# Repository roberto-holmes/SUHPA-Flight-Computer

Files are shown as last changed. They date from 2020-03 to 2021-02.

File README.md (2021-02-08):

# SUHPA Avionics

Currently divided into CRASH (Controls, Radio, and Avionics for Southampton HPA) that receives input from the pilot and sends it to Pod that controls the servos.

## Software
TODO:
- Varying frequency beep as trim value changes
- Accelerating trim input
- Add average update rate to display

Known issues:
- SD card doesn't reinitialize if it disconects as this would cause the device to only transmit packets every couple of seconds
- Packet loss is not representative of the number of packets being received by Pod as the ACK packages being sent back are the ones getting lost. Pod has to send them at a lower power for some reason causing this issue.

## Hardware

### CRASH 

v1.0
- Status: Completed
- Issues:
   * Stress relief holes for battery cables are too small
   * Middle support holes are not required
   * Circle cutout is not quite aligned
   * Square cutout could have more clearance on the left

### Pod
v1.0
- Status: Completed
- Issues: 
   * Short between 5v_Servo and GND at the BEC connector
   * Insufficient spacing between buzzer and balance connector
   * Balance connector keeps board powered (should be replaced with just measuring the voltage of V_bat)

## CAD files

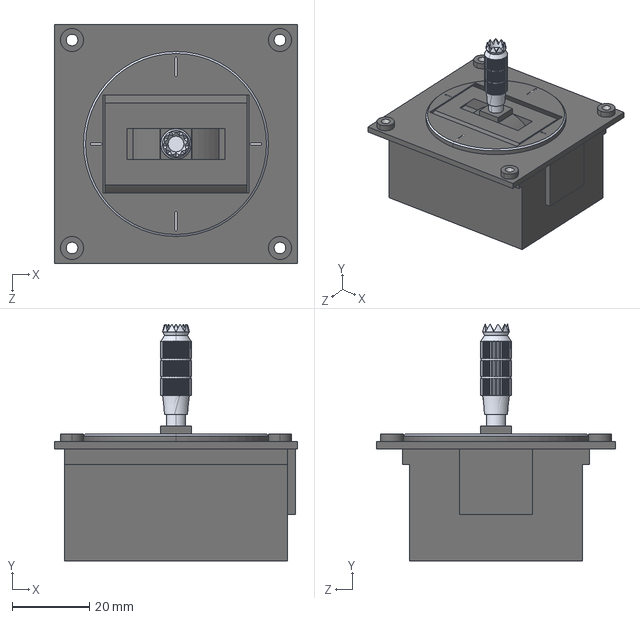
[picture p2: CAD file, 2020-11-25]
Altium/Crash/CRASH/FrSky M9 Gimbal.STEP
63.1 x 61.5 x 62.0 mm

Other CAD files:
Solidworks/FrSky M9 Gimbal.SLDPRT

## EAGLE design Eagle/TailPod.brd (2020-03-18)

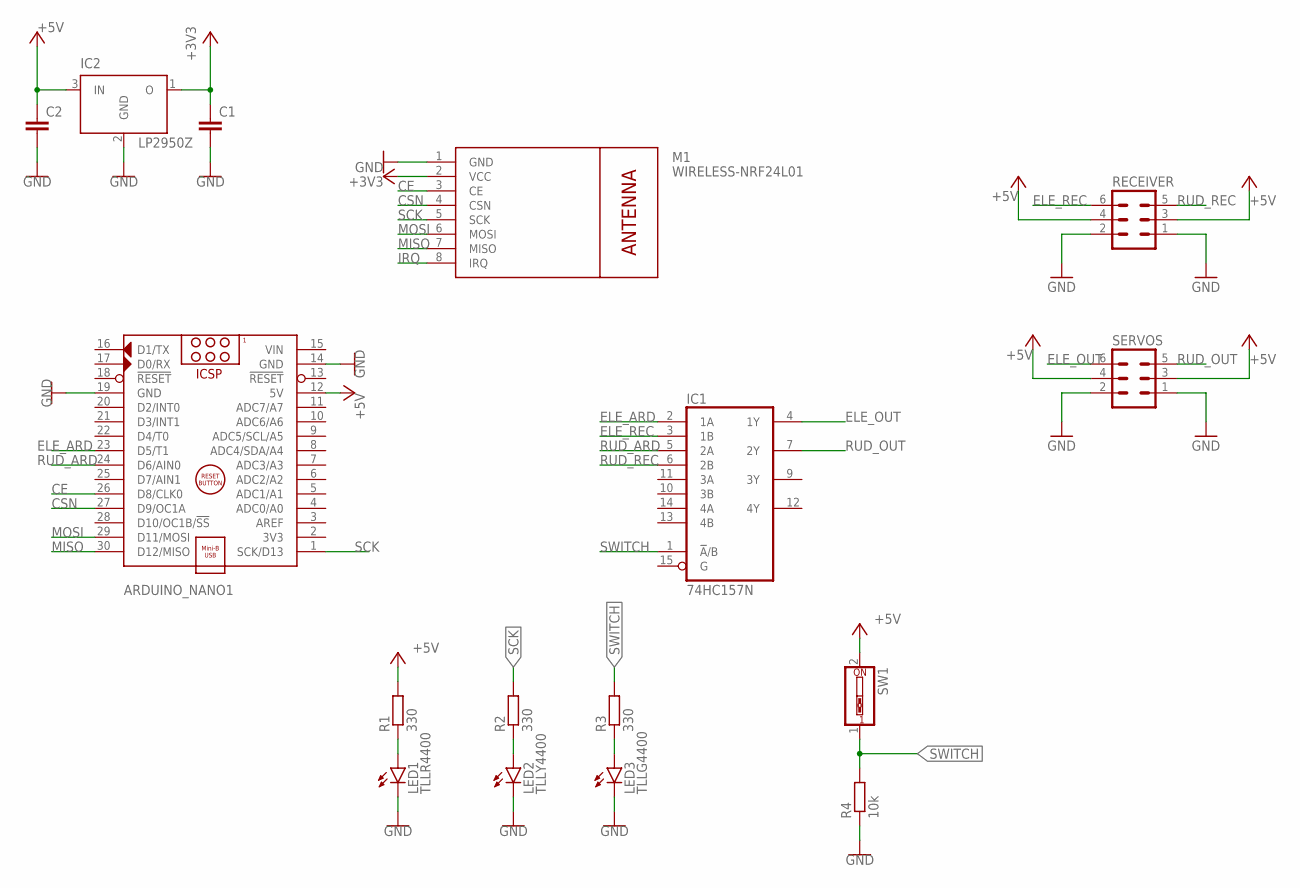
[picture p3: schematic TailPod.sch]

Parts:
ARDUINO_NANO1: ARDUINO_NANO
C1, C2: C2,5-3; C2.5-3
IC1: 74HC157N; DIL16
IC2: LP2950Z; TO92
LED1: TLLR4400; LED3MM
LED2: TLLY4400; LED3MM
LED3: TLLG4400; LED3MM
M1: WIRELESS-NRF24L01
R1, R2, R3: 330; 0204/7
R4: 10k; 0204/7
RECEIVER: MA03-2
SERVOS: MA03-2
SW1: SW_DIP-1; EDG-01

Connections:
+3V3: C1.1, IC2.1 (O), M1.2 (VCC)
+5V: ARDUINO_NANO1.12 (5V), C2.1, IC2.3 (IN), R1.2, RECEIVER.3, RECEIVER.4, SERVOS.3, SERVOS.4, SW1.2
CE: ARDUINO_NANO1.26 (D8/CLK0), M1.3 (CE)
CSN: ARDUINO_NANO1.27 (D9/OC1A), M1.4 (CSN)
ELE_ARD: ARDUINO_NANO1.23 (D5/T1), IC1.2 (1A)
ELE_OUT: IC1.4 (1Y), SERVOS.6
ELE_REC: IC1.3 (1B), RECEIVER.6
GND: ARDUINO_NANO1.14 (GND), ARDUINO_NANO1.19 (GND), C1.2, C2.2, IC1.8 (GND), IC2.2 (GND), LED1.K (C), LED2.K (C), LED3.K (C), M1.1 (GND), R4.1, RECEIVER.1, RECEIVER.2, SERVOS.1, SERVOS.2
IRQ: M1.8 (IRQ)
MISO: ARDUINO_NANO1.30 (D12/MISO), M1.7 (MISO)
MOSI: ARDUINO_NANO1.29 (D11/MOSI), M1.6 (MOSI)
unnamed: LED1.A, R1.1
unnamed: LED2.A, R2.1
unnamed: LED3.A, R3.1
RUD_ARD: ARDUINO_NANO1.24 (D6/AIN0), IC1.5 (2A)
RUD_OUT: IC1.7 (2Y), SERVOS.5
RUD_REC: IC1.6 (2B), RECEIVER.5
SCK: ARDUINO_NANO1.1 (SCK/D13), M1.5 (SCK), R2.2
SWITCH: IC1.1 (!A!/B), R3.2, R4.2, SW1.1
VCC: IC1.16 (VCC)
VIN: ARDUINO_NANO1.15 (VIN)

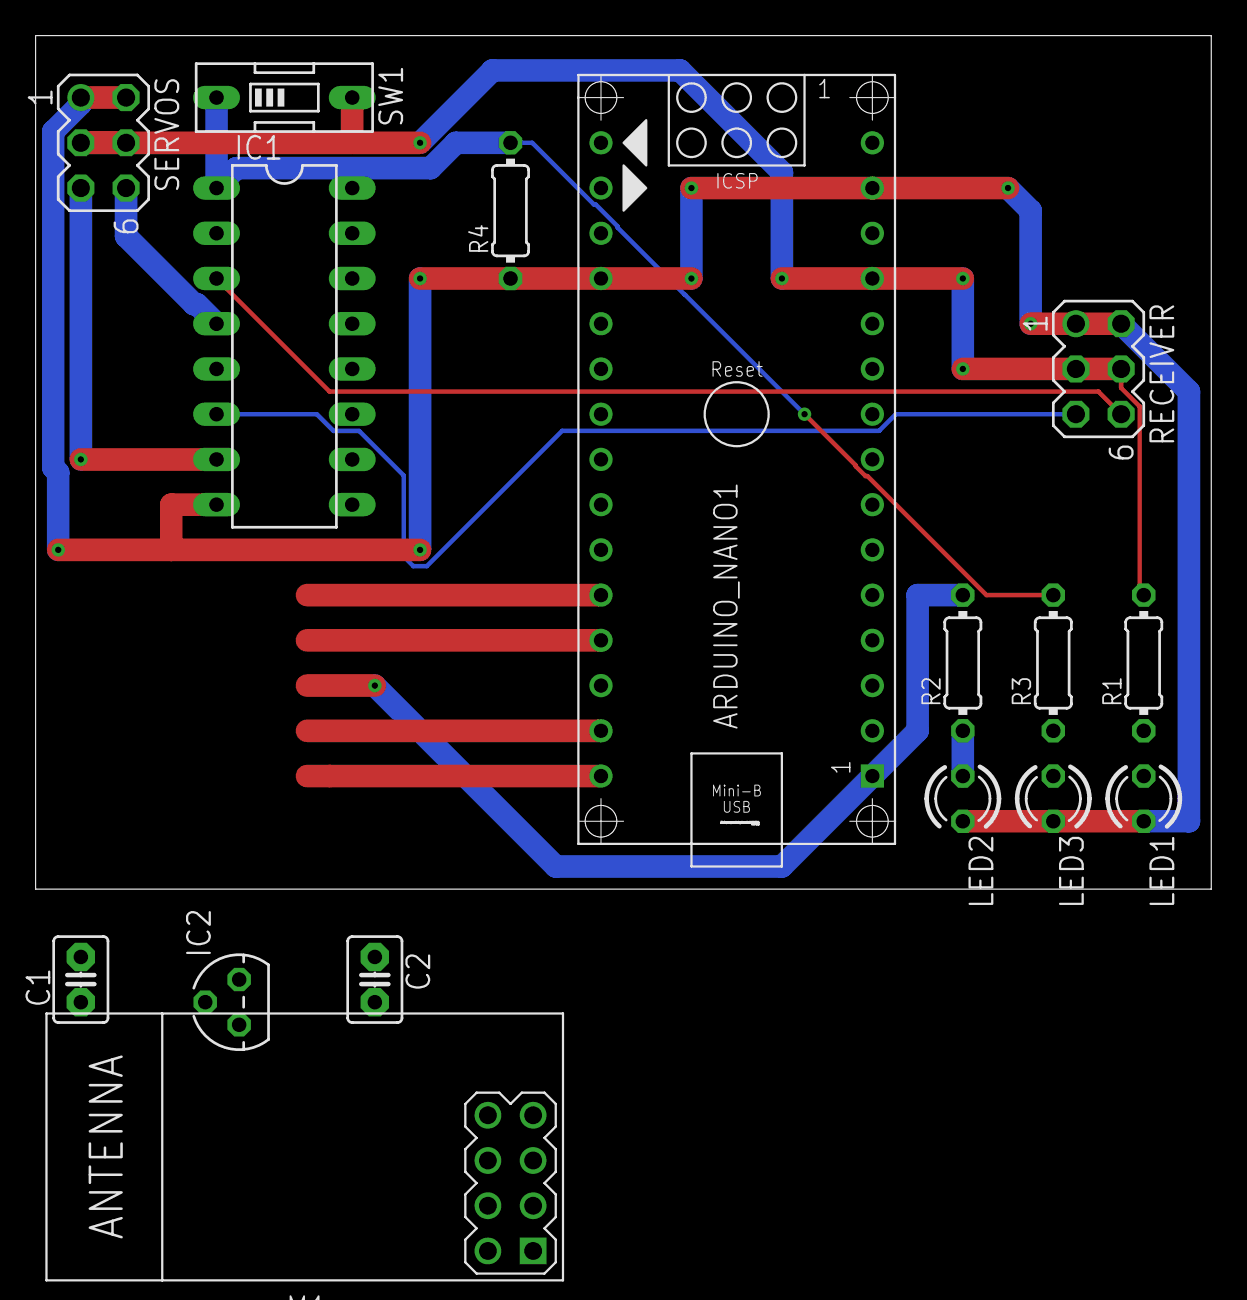
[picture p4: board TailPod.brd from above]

Board: 2 copper layers, 66.0 x 47.9 mm, 16 parts (0 on the bottom side), 18 nets.

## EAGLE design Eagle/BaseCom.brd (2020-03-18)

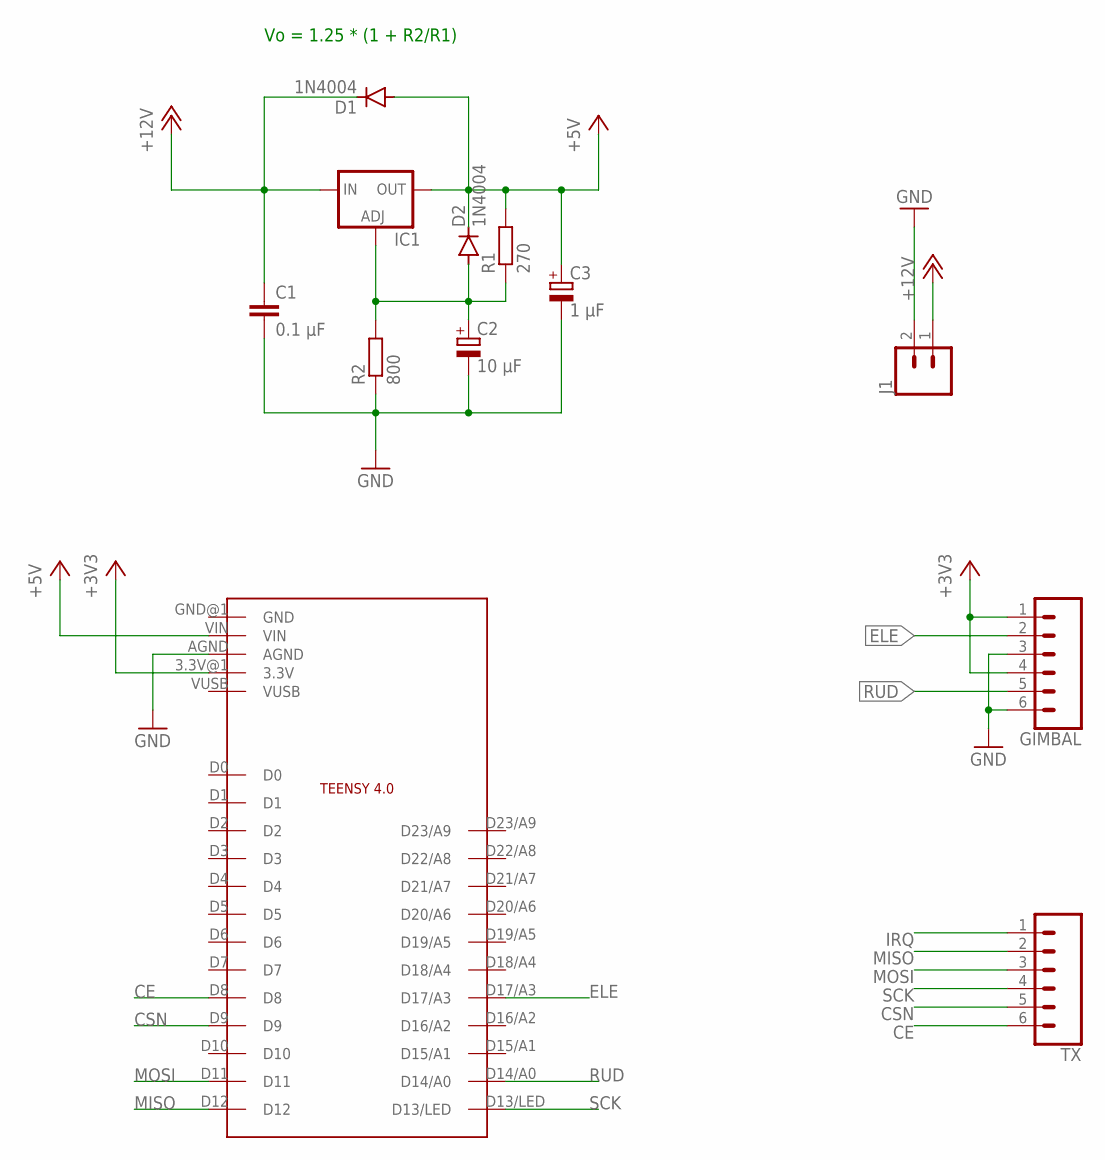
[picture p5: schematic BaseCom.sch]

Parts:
C1: 0.1 µF; C2.5-5
C2: 10 µF; E1,8-4
C3: 1 µF; E1,8-4
D1, D2: 1N4004; DO41-10
GIMBAL: CONN_06SILK_FEMALE_PTH; 1X06
IC1: LM317TL; 317TL
J1: CONN_02POLAR; MOLEX-1X2
R1: 270; 0204/7
R2: 800; 0204/7
TX: CONN_06SILK_FEMALE_PTH; 1X06
U$1: TEENSY4.0_SIMPLE

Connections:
+3V3: GIMBAL.1, GIMBAL.4, U$1.3.3V@1 (3.3V)
+5V: C3.+, D1.A, D2.C, IC1.2 (OUT), R1.2, U$1.VIN
+12V: C1.1, D1.C, IC1.3 (IN), J1.1
CE: TX.6, U$1.D8
CSN: TX.5, U$1.D9
ELE: GIMBAL.2, U$1.D17/A3
GND: C1.2, C2.-, C3.-, GIMBAL.3, GIMBAL.6, J1.2, R2.1, U$1.AGND
IRQ: TX.1
MISO: TX.2, U$1.D12
MOSI: TX.3, U$1.D11
unnamed: C2.+, D2.A, IC1.1 (ADJ), R1.1, R2.2
RUD: GIMBAL.5, U$1.D14/A0
SCK: TX.4, U$1.D13/LED

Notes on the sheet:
Vo = 1.25 * (1 + R2/R1)

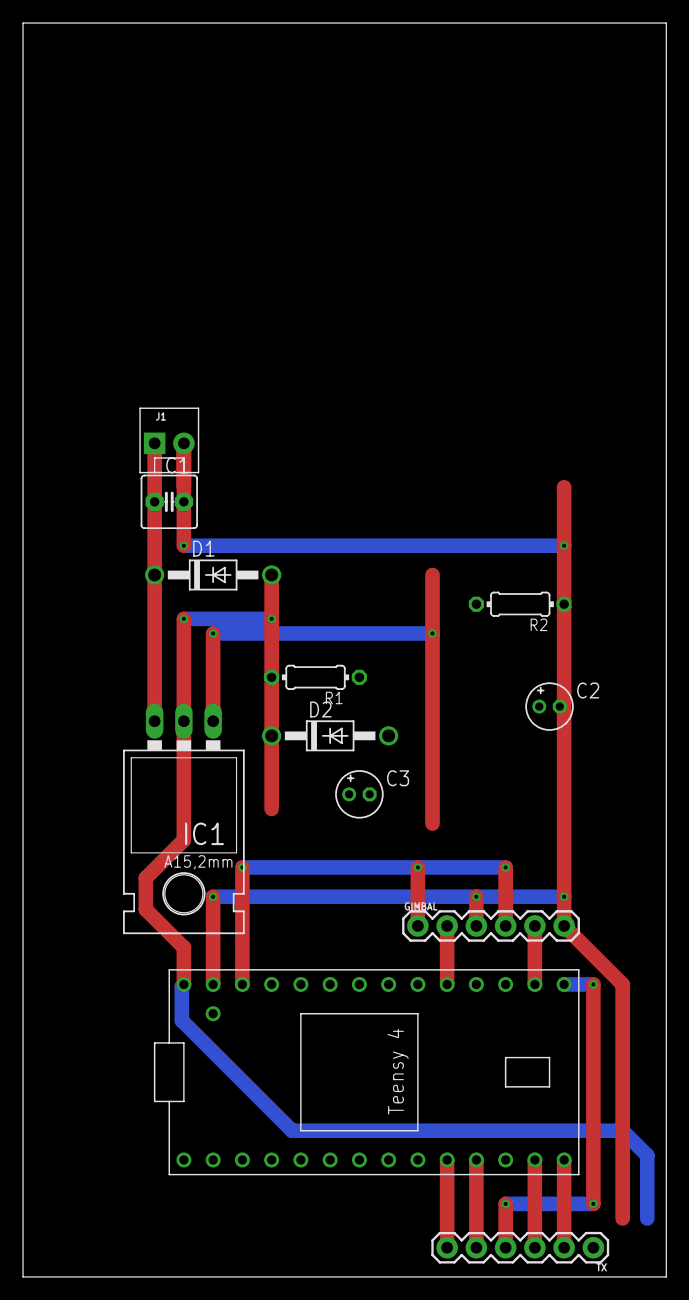
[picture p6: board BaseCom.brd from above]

Board: 2 copper layers, 55.9 x 108.9 mm, 12 parts (0 on the bottom side), 12 nets.

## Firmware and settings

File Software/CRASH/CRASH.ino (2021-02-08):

#include <Adafruit_BMP3XX.h>
#include <Adafruit_BNO055.h>
#include <EEPROM.h>
#include <RF24.h>
#include <SPI.h>
#include <SdFat.h>
#include <TimeLib.h>
#include <Wire.h>
#include <avr/pgmspace.h>
#include <math.h>
#include <nRF24L01.h>
#include <printf.h>
#include <stdint.h>
#include <usb_serial.h>
#include <util/crc16.h>

#include "Display.h"
#include "Record.h"

//#define VERBOSE_LOGGING

int leds[] = {22, 21, 40, 39, 38, 37, 35, 0, 1, 2, 3, 4};

// Trim LEDs
#define vertMin 4
#define vertLow 3
#define vertMid 2
#define vertHigh 1
#define vertMax 0

#define horizMin 40
#define horizLow 39
#define horizMid 38
#define horizHigh 37
#define horizMax 35

// Trim inputs
#define trimUp 31
#define trimDown 30

#define trimLeft 28
#define trimRight 29

// Stick inputs
#define stickVert 14
#define stickHoriz 15

// Battery voltage (If you multiply by 4.09)
#define batSense 23

// Radio
#define radioCE 27
#define radioCSN 26
#define radioINT 25
#define PACKAGE_SIZE 8
#define ACK_PAYLOAD_SIZE 2
#define PACKET_LOSS_SAMPLE_SIZE 100
#define PING_SAMPLE_SIZE 100

// Display
#define displayFR 41
#define displayCSB 16
#define displayRSTB 17
#define displayDC 20

// Other outputs
#define buzzer 33
#define led1 22
#define led2 21

// EEPROM
// There are limited write cycles to any address in EEPROM
// It should be about 100000 cycles, but in theory it could be be a problem
// If so comment out this line to dissable it
#define ENABLE_EEPROM

// You can also change to a different address as the limitation is per address not total
// Also these address need to be at least 4 apart as the trim values are integers (although they don't really need to be)
#define EEPROM_VERT_TRIM_ADDRESS 0
#define EEPROM_HORIZ_TRIM_ADDRESS 4

// Buzzer
int beepStopTime = 0;
bool beepOn = false;

// Values for battery voltage calculations
const float v100 = 3 * 4.2;
const float v0 = 3 * 3.5;
const float batVoltFactor = (3.3 * 4.09) / 1024;
float batPercent;

// PWM range (Absolute max 588 to 2400 ish)
const int vertMaxVal = 2200;
const int vertMinVal = 750;
const int horizMaxVal = 2200;
const int horizMinVal = 750;
float vertZero, horizZero;

// Stick input range
const int vertStickMax = 107;
const int vertStickMin = 910;
const int horizStickMax = 107;
const int horizStickMin = 905;
float vertStickZero, horizStickZero;

const float vertStickMultiplier = 1.0;
const float horizStickMultiplier = 1.0;
float vertStickRes, horizStickRes;

// Number of Trim steps / 2
const int vertSteps = 99;
const int horizSteps = 99;
float vertRes, horizRes;

// Values to store Trim and PWM
int vertTrim = 0;
int horizTrim = 0;
int vertVal = 0;
int horizVal = 0;

// Store state of trim buttons
bool trimUpDown = false;
bool trimDownDown = false;
bool trimLeftDown = false;
bool trimRightDown = false;

// Values for debouncing
unsigned long trimUpLastDebounceTime = 0;
unsigned long trimDownLastDebounceTime = 0;
unsigned long trimLeftLastDebounceTime = 0;
unsigned long trimRightLastDebounceTime = 0;

unsigned long trimUpLastPressTime = 0;
unsigned long trimDownLastPressTime = 0;
unsigned long trimLeftLastPressTime = 0;
unsigned long trimRightLastPressTime = 0;

const unsigned long debounceDelay = 50;
const unsigned long holdDelay = 250;
const unsigned long holdDelayCentre = 500;

// Radio Setup
RF24 radio(radioCE, radioCSN);
uint8_t address[][6] = {"CRASH", "Poddd"};
byte package[PACKAGE_SIZE];

// Variables frequency of communication
const unsigned long txInterval = 10;
unsigned long lastTXMillis;

// Control when the display gets updated
const unsigned long displayUpdateInterval = 20;
unsigned long lastDisplayUpdateMillis;

// Variables for calculating packet loss
bool ack[PACKET_LOSS_SAMPLE_SIZE];
int ackPos = 0;
int truers = 0;
float packetLoss;  // Fraction of packets that don't receive ack

// Variables for calculating return trip time
unsigned long pingArray[PACKET_LOSS_SAMPLE_SIZE];
int pingPos = 0;
float ping;	 // Average return trip time in ms

// Sensors
#define IMU_I2C_ADDRESS BNO055_ADDRESS_A
Adafruit_BNO055 imuDevice = Adafruit_BNO055(0, IMU_I2C_ADDRESS);
Adafruit_BMP3XX barometerDevice = Adafruit_BMP3XX();
DataRecord currentSensorData;
const unsigned long sensorReadInterval = 50;
unsigned long lastSensorUpdateMillis;

// Storage
#define STORAGE_DATA_DIRECTORY "Data"
#define STORAGE_FILE_NAME_FORMAT "Data/XXXX.csv\0"
#define STORAGE_FILE_NAME_LENGTH 14
#define STORAGE_FILE_NAME_NUMBER_START 5
#define STORAGE_FILE_NAME_MAX_NUMBER 9999

SdExFat sdio;
ExFile sdFile;
char* fileName = NULL;
bool sdCardInitialised = false;
SdioConfig sdConfig = SdioConfig();

// the setup routine runs once when you press reset:
void setup()
{
	Display::Init();
	initSensors();
	initSD();

	pinMode(vertMin, OUTPUT);
	pinMode(vertLow, OUTPUT);
	pinMode(vertMid, OUTPUT);
	pinMode(vertHigh, OUTPUT);
	pinMode(vertMax, OUTPUT);

	pinMode(horizMin, OUTPUT);
	pinMode(horizLow, OUTPUT);
	pinMode(horizMid, OUTPUT);
	pinMode(horizHigh, OUTPUT);
	pinMode(horizMax, OUTPUT);
	pinMode(buzzer, OUTPUT);

	pinMode(trimUp, INPUT);
	pinMode(trimDown, INPUT);
	pinMode(trimLeft, INPUT);
	pinMode(trimRight, INPUT);

	pinMode(stickVert, INPUT);
	pinMode(stickHoriz, INPUT);

	pinMode(batSense, INPUT);

	// Ensure trim LEDs are off
	digitalWrite(vertMin, LOW);
	digitalWrite(vertLow, LOW);
	digitalWrite(vertMid, LOW);
	digitalWrite(vertHigh, LOW);
	digitalWrite(vertMax, LOW);
	digitalWrite(horizMin, LOW);
	digitalWrite(horizLow, LOW);
	digitalWrite(horizMid, LOW);
	digitalWrite(horizHigh, LOW);
	digitalWrite(horizMax, LOW);

	pinMode(led1, OUTPUT);
	pinMode(led2, OUTPUT);
	pinMode(13, OUTPUT);

	for (int i = 0; i < 11; i++)
	{
		digitalWrite(leds[i], HIGH);
		delay(100);
		digitalWrite(leds[i], LOW);
	}

	for (int i = 12 - 1; i >= 1; i--)
	{
		digitalWrite(leds[i], HIGH);
		delay(100);
		digitalWrite(leds[i], LOW);
	}

	digitalWrite(leds[0], HIGH);
	delay(200);
	digitalWrite(leds[0], LOW);

	vertRes = (vertMaxVal - vertMinVal) / (2.0 * (vertSteps));
	horizRes = (horizMaxVal - horizMinVal) / (2.0 * (horizSteps));

	vertStickZero = (vertStickMax + vertStickMin) / 2.0;
	horizStickZero = (horizStickMax + horizStickMin) / 2.0;

	vertZero = (vertMaxVal + vertMinVal) / 2.0;
	horizZero = (horizMaxVal + horizMinVal) / 2.0;

	vertStickRes = vertStickMultiplier * (vertMaxVal - vertMinVal) / 2.0;
	horizStickRes = horizStickMultiplier * (horizMaxVal - horizMinVal) / 2.0;

	// Radio is not responding -> turn on warning LED
	if (!radio.begin())
	{
		digitalWrite(led2, HIGH);
	}

	// Initialise ack array
	for (int i = 0; i < PACKET_LOSS_SAMPLE_SIZE; i++)
		ack[i] = true;

	radio.setPALevel(RF24_PA_MAX);

	// Set up ack payloads
	radio.enableDynamicPayloads();
	radio.enableAckPayload();

	// Set up pipes
	radio.openWritingPipe(address[0]);
	radio.openReadingPipe(1, address[1]);

	// Put radio in TX mode
	radio.stopListening();

	lastTXMillis = millis();
	lastSensorUpdateMillis = millis();
	lastDisplayUpdateMillis = millis();

	readFromEEPROM();

	updateVertTrim(0);
	updateHorizTrim(0);
}

//uint32_t lastTime = 0;
//int counter = 0;

// the loop routine runs over and over again forever:
void loop()
{
	// Use the test how often the loop updates
	// counter++;
	// if (counter >= 100)
	// {
	// 	uint32_t currentTime = millis ();
	// 	Serial.println ((currentTime - lastTime) / counter);
	// 	lastTime = currentTime;
	// 	counter = 0;
	// }

	// Asynchronous beep
	if (beepOn && millis () >= (uint32_t)beepStopTime)
	{
		analogWrite (buzzer, 0);
		beepOn = false;
	}

	// Calculate battery state
	float batVoltage = analogRead(batSense) * batVoltFactor;
	batPercent = constrain(map(batVoltage, v0, v100, 0.0, 1.0), 0.0, 1.0);
	if (batPercent < .25)
		digitalWrite(led1, HIGH);
	else
		digitalWrite(led1, LOW);

	// Read Stick inputs and normalise
	float vertStickValue = -2.0 * (analogRead(stickVert) - vertStickZero) / (vertStickMax - vertStickMin);
	float horizStickValue = 2.0 * (analogRead(stickHoriz) - horizStickZero) / (horizStickMax - horizStickMin);

	// Calculate PWM values in both axis by combining stick inputs with trim
	float tempVertVal = vertStickValue * vertStickRes - vertTrim * vertRes + vertZero;
	float tempHorizVal = horizStickValue * horizStickRes - horizTrim * horizRes + horizZero;

	vertStickValue = constrain(vertStickValue, -1, 1);
	horizStickValue = constrain(horizStickValue, -1, 1);

	vertVal = constrain(tempVertVal, vertMinVal, vertMaxVal);
	horizVal = constrain(tempHorizVal, horizMinVal, horizMaxVal);

	// Check if button is being pressed
	if (digitalRead(trimUp))
	{
		// Debounce and check if the button is being held down
		if ((!trimUpDown || (vertTrim != 0 && millis() > trimUpLastPressTime + holdDelay) || (vertTrim == 0 && millis() > trimUpLastPressTime + holdDelayCentre)) && millis() > trimUpLastPressTime + debounceDelay)
		{
			trimUpLastPressTime = millis();
			trimUpDown = true;
			// vertTrim++;
			updateVertTrim(1);
		}
	}
	else
	{
		trimUpDown = false;
	}

	if (digitalRead(trimDown))
	{
		if ((!trimDownDown || (vertTrim != 0 && millis() > trimDownLastPressTime + holdDelay) || (vertTrim == 0 && millis() > trimDownLastPressTime + holdDelayCentre)) && millis() > trimDownLastPressTime + debounceDelay)
		{
			trimDownLastPressTime = millis();
			trimDownDown = true;
			// vertTrim--;
			updateVertTrim(-1);
		}
	}
	else
	{
		trimDownDown = false;
	}

	if (digitalRead(trimLeft))
	{
		if ((!trimLeftDown || (horizTrim != 0 && millis() > trimLeftLastPressTime + holdDelay) || (horizTrim == 0 && millis() > trimLeftLastPressTime + holdDelayCentre)) && millis() > trimLeftLastPressTime + debounceDelay)
		{
			trimLeftLastPressTime = millis();
			trimLeftDown = true;
			// horizTrim--;
			updateHorizTrim(-1);
		}
	}
	else
	{
		trimLeftDown = false;
	}

	if (digitalRead(trimRight))
	{
		if ((!trimRightDown || (horizTrim != 0 && millis() > trimRightLastPressTime + holdDelay) || (horizTrim == 0 && millis() > trimRightLastPressTime + holdDelayCentre)) && millis() > trimRightLastPressTime + debounceDelay)
		{
			trimRightLastPressTime = millis();
			trimRightDown = true;
			// horizTrim++;
			updateHorizTrim(1);
		}
	}
	else
	{
		trimRightDown = false;
	}

	unsigned long currentMillis = millis();

	// Decide whether it is time to transmit
	if (currentMillis - lastTXMillis > txInterval)
	{
		lastTXMillis = currentMillis;
		// Transmit PWM values
		transmit(vertVal, horizVal);
	}

	// Decide whether it is time to update screen
	if (currentMillis - lastDisplayUpdateMillis > displayUpdateInterval)
	{
		lastDisplayUpdateMillis = currentMillis;
		Display::Update(vertVal, horizVal, horizMinVal, horizMaxVal, vertMinVal, vertMaxVal, horizTrim, vertTrim, batPercent, ping, packetLoss, sdCardInitialised);
	}

	// Decide whether it is time to read and save sensor data
	if (currentMillis - lastSensorUpdateMillis > sensorReadInterval)
	{
		lastSensorUpdateMillis = currentMillis;

		// Read sensor data
		readFromSensors();

		// Use to print data to console
		//currentSensorData.printData ();

		// Save the data to SD card
		saveCurrentDataRecord();
	}
}

void beep(int level, int time)
{
	analogWrite(buzzer, 64 + (level * 16));
	beepStopTime = millis() + time;
	beepOn = true;
}

void updateVertTrim(int trimInput)
{
	if (trimInput != 0)
	{
		if (vertTrim + trimInput <= vertSteps && vertTrim + trimInput >= -vertSteps)
		{
			vertTrim += trimInput;
			beep(0, 100);
		}
	}

	digitalWrite(vertMin, LOW);
	digitalWrite(vertLow, LOW);
	digitalWrite(vertMid, LOW);
	digitalWrite(vertHigh, LOW);
	digitalWrite(vertMax, LOW);

	if (vertTrim == -vertSteps)
		digitalWrite(vertMin, HIGH);
	else if (vertTrim < 0)
		digitalWrite(vertLow, HIGH);
	else if (vertTrim == 0)
		digitalWrite(vertMid, HIGH);
	else if (vertTrim < vertSteps)
		digitalWrite(vertHigh, HIGH);
	else if (vertTrim == vertSteps)
		digitalWrite(vertMax, HIGH);

	writeToEEPROM();
}

void updateHorizTrim(int trimInput)
{
	if (trimInput != 0)
	{
		if (horizTrim + trimInput <= horizSteps && horizTrim + trimInput >= -horizSteps)
		{
			horizTrim += trimInput;
			beep(0, 100);
		}
	}

	digitalWrite(horizMin, LOW);
	digitalWrite(horizLow, LOW);
	digitalWrite(horizMid, LOW);
	digitalWrite(horizHigh, LOW);
	digitalWrite(horizMax, LOW);

	if (horizTrim == -horizSteps)
		digitalWrite(horizMin, HIGH);
	else if (horizTrim < 0)
		digitalWrite(horizLow, HIGH);
	else if (horizTrim == 0)
		digitalWrite(horizMid, HIGH);
	else if (horizTrim < horizSteps)
		digitalWrite(horizHigh, HIGH);
	else if (horizTrim == horizSteps)
		digitalWrite(horizMax, HIGH);

	writeToEEPROM();
}

void transmit(float ele, float rud)
{
	memcpy(package + 0, &ele, 4);
	memcpy(package + 4, &rud, 4);

	unsigned long start_timer = micros();  // start the timer
	bool report = radio.write(&package, PACKAGE_SIZE);	// transmit & save the report
	unsigned long end_timer = micros();	 // end the timer

	if (report)
	{
		//Serial.print(F("Transmission successful! "));  // payload was delivered
		// Serial.print(F("Time to transmit = "));
		// Serial.println(end_timer - start_timer);  // print the timer result
		// Serial.print(F(" us. Sent: "));
		// Serial.println(payload);	// print the outgoing message

		ack[ackPos] = true;
		pingArray[pingPos++] = end_timer - start_timer;
		pingPos %= PING_SAMPLE_SIZE;

		uint8_t pipe;
		if (radio.available(&pipe))
		{  // is there an ACK payload? grab the pipe number that received it
			byte received[ACK_PAYLOAD_SIZE];
			radio.read(&received, sizeof(received));  // get incoming ACK payload
			// Serial.print(F(" Received "));
			// Serial.print(radio.getDynamicPayloadSize());  // print incoming payload size
			// Serial.print(F(" bytes on pipe "));
			// Serial.print(pipe);	 // print pipe number that received the ACK
			// Serial.print(F(": "));
			// Serial.println(received);
		}
		else
		{
#if VERBOSE_LOGGING
			Serial.println (F ("Received: an empty ACK packet, ")); // empty ACK packet received
#endif
		}
	}
	else
	{
#if VERBOSE_LOGGING
		Serial.println (F ("Transmission failed or timed out, ")); // payload was not delivered
#endif
		ack[ackPos] = false;
	}

	// Calculate average ping over sample size
	ping = 0;
	for (int i = 0; i < PING_SAMPLE_SIZE; i++)
		ping += pingArray[i];
	ping /= (float)PING_SAMPLE_SIZE;
	ping /= 1000.;	// Convert from us to ms;

	// Calculate packet loss over sample size
	++ackPos %= PACKET_LOSS_SAMPLE_SIZE;
	truers = 0;
	for (int i = 0; i < PACKET_LOSS_SAMPLE_SIZE; i++)
	{
		if (ack[i])
			truers++;
	}
	packetLoss = 1 - (float)truers / (float)PACKET_LOSS_SAMPLE_SIZE;

	//Serial.print("Packet Loss: ");
	//Serial.print(packetLoss);
	//Serial.print(", Ping: ");
	//Serial.println(ping);
}

void readFromEEPROM()
{
#ifdef ENABLE_EEPROM

	// Read in the values
	vertTrim = readIntToEEPROM(EEPROM_VERT_TRIM_ADDRESS);
	horizTrim = readIntToEEPROM(EEPROM_HORIZ_TRIM_ADDRESS);

	// Validate the values
	// If they are not correct, give them default values
	// This is needed if the EEPROM gets corrupted
	if (vertTrim > vertSteps || vertTrim < -vertSteps) vertTrim = 0;
	if (horizTrim > horizSteps || horizTrim < -horizSteps) horizTrim = 0;

#endif	// ENABLE_EEPROM
}

void writeToEEPROM()
{
#ifdef ENABLE_EEPROM

	writeIntToEEPROM(EEPROM_VERT_TRIM_ADDRESS, vertTrim);
	writeIntToEEPROM(EEPROM_HORIZ_TRIM_ADDRESS, horizTrim);

#endif	// ENABLE_EEPROM
}

void writeIntToEEPROM(int address, int value)
{
	// Use the update method, so that we don't write to the EEPROM unless it is needed
	EEPROM.update(address + 0, (byte)(value));
	EEPROM.update(address + 1, (byte)(value >> 8));
	EEPROM.update(address + 2, (byte)(value >> 16));
	EEPROM.update(address + 3, (byte)(value >> 24));
}

int readIntToEEPROM(int address)
{
	int value = 0;

	value |= EEPROM.read(address);
	value |= EEPROM.read(address + 1) << 8;
	value |= EEPROM.read(address + 2) << 16;
	value |= EEPROM.read(address + 3) << 24;

	return value;
}

void initSensors()
{
	imuInit();
	barometerInit();
}

void readFromSensors()
{
	currentSensorData.time = millis();
	currentSensorData.vertVal = vertVal;
	currentSensorData.horizVal = horizVal;
	currentSensorData.vertTrim = vertTrim;
	currentSensorData.horizTrim = horizTrim;
	currentSensorData.ping = ping;
	currentSensorData.packetLoss = packetLoss;
	currentSensorData.batteryPercent = batPercent;
	imuRead();
	barometerRead();
}

bool imuInit()
{
	if (!imuDevice.begin(Adafruit_BNO055::adafruit_bno055_opmode_t::OPERATION_MODE_NDOF)) return false;

	//imuDevice.setAxisRemap (Adafruit_BNO055::adafruit_bno055_axis_remap_config_t::REMAP_CONFIG_P3);
	//imuDevice.setAxisSign (Adafruit_BNO055::adafruit_bno055_axis_remap_sign_t::REMAP_SIGN_P3);
	imuDevice.setExtCrystalUse(true);
	imuDevice.enterNormalMode();

	//while (!imuDevice.isFullyCalibrated ()) delay (10);

#ifdef VERBOSE_LOGGING
	Serial.println("BNO055 Configured");
#endif	// VERBOSE_LOGGING
	return true;
}

bool barometerInit()
{
	if (!barometerDevice.begin_I2C()) return false;

	// Configure device
	if (!barometerDevice.setTemperatureOversampling(BMP3_OVERSAMPLING_2X)) return false;
	if (!barometerDevice.setPressureOversampling(BMP3_OVERSAMPLING_8X)) return false;
	if (!barometerDevice.setIIRFilterCoeff(BMP3_IIR_FILTER_COEFF_3)) return false;
	if (!barometerDevice.setOutputDataRate(BMP3_ODR_50_HZ)) return false;

#ifdef VERBOSE_LOGGING
	Serial.println("BMP388 Configured");
#endif	// VERBOSE_LOGGING
	return true;
}

bool imuRead()
{
	sensors_event_t imuEvent;
	imuDevice.getEvent(&imuEvent, Adafruit_BNO055::VECTOR_ACCELEROMETER);
	currentSensorData.acceleration[0] = imuEvent.acceleration.x;
	currentSensorData.acceleration[1] = imuEvent.acceleration.y;
	currentSensorData.acceleration[2] = imuEvent.acceleration.z;
	imuDevice.getEvent(&imuEvent, Adafruit_BNO055::VECTOR_MAGNETOMETER);
	currentSensorData.mag[0] = imuEvent.magnetic.x;
	currentSensorData.mag[1] = imuEvent.magnetic.y;
	currentSensorData.mag[2] = imuEvent.magnetic.z;
	imuDevice.getEvent(&imuEvent, Adafruit_BNO055::VECTOR_GYROSCOPE);
	currentSensorData.gyro[0] = imuEvent.gyro.x * DEG_TO_RAD;
	currentSensorData.gyro[1] = imuEvent.gyro.y * DEG_TO_RAD;
	currentSensorData.gyro[2] = imuEvent.gyro.z * DEG_TO_RAD;
	imuDevice.getEvent(&imuEvent, Adafruit_BNO055::VECTOR_GRAVITY);
	currentSensorData.gravity[0] = imuEvent.acceleration.x;
	currentSensorData.gravity[1] = imuEvent.acceleration.y;
	currentSensorData.gravity[2] = imuEvent.acceleration.z;
	imuDevice.getEvent(&imuEvent, Adafruit_BNO055::VECTOR_LINEARACCEL);
	currentSensorData.linearAcceleration[0] = imuEvent.acceleration.x;
	currentSensorData.linearAcceleration[1] = imuEvent.acceleration.y;
	currentSensorData.linearAcceleration[2] = imuEvent.acceleration.z;

	// Orientation is given as heading roll pitch, rather than as rotations around x y z axis
	// As such
	//	x := pitch
	//	y:= roll
	//	z:= heading
	// We then also need to remap to have the correct ranges of angles
	imuDevice.getEvent(&imuEvent, Adafruit_BNO055::VECTOR_EULER);
	currentSensorData.orientation[0] = imuEvent.orientation.z * DEG_TO_RAD;
	currentSensorData.orientation[1] = imuEvent.orientation.y * DEG_TO_RAD;
	currentSensorData.orientation[2] = imuEvent.orientation.x * DEG_TO_RAD;
	// currentSensorData.orientation[0] = HALF_PI + (imuEvent.orientation.z * DEG_TO_RAD);
	// currentSensorData.orientation[1] = (imuEvent.orientation.y * DEG_TO_RAD) - PI;
	// currentSensorData.orientation[2] = (imuEvent.orientation.x * DEG_TO_RAD) - PI;

	// if (currentSensorData.orientation[0] < 0)
	// {
	// 	currentSensorData.orientation[0] = -currentSensorData.orientation[0];
	// 	currentSensorData.orientation[1] += PI;
	// 	currentSensorData.orientation[2] += PI;
	// }

	// if (currentSensorData.orientation[0] > PI)
	// {
	// 	currentSensorData.orientation[0] = TWO_PI - currentSensorData.orientation[0];
	// 	currentSensorData.orientation[1] += PI;
	// 	currentSensorData.orientation[2] += PI;
	// }

	// currentSensorData.orientation[1] -= floor (currentSensorData.orientation[1] / TWO_PI) * TWO_PI;
	// currentSensorData.orientation[1] -= PI;
	// currentSensorData.orientation[1] = -currentSensorData.orientation[1];

	// currentSensorData.orientation[2] -= floor (currentSensorData.orientation[2] / TWO_PI) * TWO_PI;
	// currentSensorData.orientation[2] -= PI;

	return true;
}

bool barometerRead()
{
	if (!barometerDevice.performReading()) return false;

	currentSensorData.pressure = barometerDevice.readPressure ();
	currentSensorData.temperature = barometerDevice.readTemperature();

	return true;
}

bool isFile()
{
	return fileName != NULL;
}

void startNewFile()
{
	if (!sdCardInitialised) initSD();
	if (sdCardInitialised)
	{
		findNextFileName();

		// Make sure there is a Data folder
		if (!sdFile.open(STORAGE_DATA_DIRECTORY, O_CREAT))
		{
#ifdef VERBOSE_LOGGING
			Serial.print("Failed to open directory with error: ");
			Serial.println(sdFile.getError());
#endif
			sdCardInitialised = false;
			return;
		}
		else
		{
			sdFile.close();
		}

		if (!sdFile.open(fileName, O_APPEND | O_RDWR | O_CREAT))
		{
#ifdef VERBOSE_LOGGING
			Serial.print("Failed to open file with error: ");
			Serial.println(sdFile.getError());
#endif
			sdCardInitialised = false;
			return;
		}
		else
		{
			currentSensorData.saveHeader(&sdFile);
			sdFile.close();
		}

#ifdef VERBOSE_LOGGING
		Serial.print("Created new file: ");
		Serial.println(fileName);
#endif
	}
}

void findNextFileName()
{
	if (fileName == NULL) fileName = (char*)malloc(STORAGE_FILE_NAME_LENGTH);
	memcpy(fileName, STORAGE_FILE_NAME_FORMAT, STORAGE_FILE_NAME_LENGTH);

	for (int i = 0; i <= STORAGE_FILE_NAME_MAX_NUMBER; i++)
	{
		setFileName(i);
		if (!sdio.exists(fileName)) return;
	}

#ifdef VERBOSE_LOGGING
	Serial.println("Reached maximum number of files");
#endif
}
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

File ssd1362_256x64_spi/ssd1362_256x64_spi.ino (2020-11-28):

/**************************************************************************
 This is an example for our Monochrome OLEDs based on SSD1362 drivers

 Pick one up today in the adafruit shop!
 ------> http://www.adafruit.com/category/63_98

 This example is for a 256x64 pixel display using SPI to communicate
 4 or 5 pins are required to interface.

 Adafruit invests time and resources providing this open
 source code, please support Adafruit and open-source
 hardware by purchasing products from Adafruit!

 Written by Limor Fried/Ladyada for Adafruit Industries,
 with contributions from the open source community.
 BSD license, check license.txt for more information
 All text above, and the splash screen below must be
 included in any redistribution.
 **************************************************************************/

#include <Adafruit_GFX.h>
#include <SPI.h>
#include <Wire.h>

#include "Adafruit_SSD1362.h"
#include "suhpaLogo.h"

#define SCREEN_WIDTH 256 // OLED display width, in pixels
#define SCREEN_HEIGHT 64 // OLED display height, in pixels

// Declaration for SSD1362 display connected using software SPI (default case):
/*#define OLED_MOSI   11
#define OLED_CLK   13
#define OLED_DC    41
#define OLED_CS    17
#define OLED_RESET 16
Adafruit_SSD1362 display(SCREEN_WIDTH, SCREEN_HEIGHT,
  OLED_MOSI, OLED_CLK, OLED_DC, OLED_RESET, OLED_CS);
*/

//Comment out above, uncomment this block to use hardware SPI
#define OLED_DC 41
#define OLED_CS 17
#define OLED_RESET 16
#define OLED_FR 20
Adafruit_SSD1362 display (SCREEN_WIDTH, SCREEN_HEIGHT, &SPI, OLED_DC, OLED_RESET, OLED_CS);

#define NUMFLAKES 10 // Number of snowflakes in the animation example

#define LOGO_HEIGHT 16
#define LOGO_WIDTH 16
static const unsigned char PROGMEM logo_bmp[] = { B00000000, B11000000, B00000001, B11000000, B00000001, B11000000, B00000011, B11100000, B11110011, B11100000, B11111110, B11111000, B01111110, B11111111, B00110011, B10011111, B00011111, B11111100, B00001101, B01110000, B00011011, B10100000, B00111111, B11100000, B00111111, B11110000, B01111100, B11110000, B01110000, B01110000, B00000000, B00110000 };

void setup ()
{
	Serial.begin (9600);

	//while (!Serial.dtr ());

	pinMode (OLED_FR, INPUT);
	//pinMode (2, OUTPUT);
	//pinMode (38, OUTPUT);

	// SSD1362_SWITCHCAPVCC = generate display voltage from 3.3V internally
	if (!display.begin (SSD1362_EXTERNALVCC))
	{
		Serial.println (F ("SSD1362 allocation failed"));
		for (;;)
			; // Don't proceed, loop forever
	}

	display.clearDisplay ();
	display.drawBitmap ((display.width () - SUHPALogo_width) / 2, (display.height () - SUHPALogo_height) / 2, SUHPALogo_data, SUHPALogo_width, SUHPALogo_height, SSD1362_WHITE);
	display.display ();
	delay (500); // Pause for 2 seconds

	// // Clear the buffer
	// display.clearDisplay ();

	// // Draw a single pixel in white
	// display.drawPixel (10, 10, SSD1362_WHITE);

	// // Show the display buffer on the screen. You MUST call display() after
	// // drawing commands to make them visible on screen!
	// display.display ();
	// delay (200);
	// // display.display()
	// // is NOT necessary after every single drawing command,
	// //unless that's what you want...rather, you can batch up a bunch of
	// //drawing operations and then update the screen all at once by calling
	// // display.display(). These examples demonstrate both approaches...

	// testdrawline (); // Draw many lines

	// testdrawrect (); // Draw rectangles (outlines)

	// testfillrect (); // Draw rectangles (filled)

	// testdrawcircle (); // Draw circles (outlines)

	// testfillcircle (); // Draw circles (filled)

	// testdrawroundrect (); // Draw rounded rectangles (outlines)

	// testfillroundrect (); // Draw rounded rectangles (filled)

	// testdrawtriangle (); // Draw triangles (outlines)

	// testfilltriangle (); // Draw triangles (filled)

	// testdrawchar (); // Draw characters of the default font

	// testdrawstyles (); // Draw 'stylized' characters

	// testscrolltext (); // Draw scrolling text

	// testdrawbitmap (); // Draw a small bitmap image

	// // Invert and restore display, pausing in-between
	// // display.invertDisplay (true);
	// // delay (1500);
	// // display.invertDisplay (false);
	// // delay (500);
	// //display.invertDisplay (true);
	// testanimate (logo_bmp, LOGO_WIDTH, LOGO_HEIGHT); // Animate bitmaps

	// display.clearDisplay ();
}

uint8_t offset = 128;

void loop ()
{
	display.clearDisplay ();

	display.drawBitmap ((display.width () - SUHPALogo_width) / 2 + 256 + ((offset * 3) / 2) - 128, -16 + (display.height () - SUHPALogo_height) / 2, SUHPALogo_data, SUHPALogo_width, SUHPALogo_height, SSD1362_WHITE / 4);
	display.drawBitmap ((display.width () - SUHPALogo_width) / 2 - 000 + ((offset * 3) / 2) - 128, -16 + (display.height () - SUHPALogo_height) / 2, SUHPALogo_data, SUHPALogo_width, SUHPALogo_height, SSD1362_WHITE / 4);
	display.drawBitmap ((display.width () - SUHPALogo_width) / 2 - 256 + ((offset * 3) / 2) - 128, -16 + (display.height () - SUHPALogo_height) / 2, SUHPALogo_data, SUHPALogo_width, SUHPALogo_height, SSD1362_WHITE / 4);
	display.drawBitmap ((display.width () - SUHPALogo_width) / 2 + 384 + ((offset * 3) / 2) - 128, -16 + (display.height () - SUHPALogo_height) / 2, SUHPALogo_data, SUHPALogo_width, SUHPALogo_height, SSD1362_WHITE / 4);
	display.drawBitmap ((display.width () - SUHPALogo_width) / 2 + 128 + ((offset * 3) / 2) - 128, -16 + (display.height () - SUHPALogo_height) / 2, SUHPALogo_data, SUHPALogo_width, SUHPALogo_height, SSD1362_WHITE / 4);
	display.drawBitmap ((display.width () - SUHPALogo_width) / 2 - 128 + ((offset * 3) / 2) - 128, -16 + (display.height () - SUHPALogo_height) / 2, SUHPALogo_data, SUHPALogo_width, SUHPALogo_height, SSD1362_WHITE / 4);
	display.drawBitmap ((display.width () - SUHPALogo_width) / 2 - 384 + ((offset * 3) / 2) - 128, -16 + (display.height () - SUHPALogo_height) / 2, SUHPALogo_data, SUHPALogo_width, SUHPALogo_height, SSD1362_WHITE / 4);
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

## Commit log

2020-03-18 Added stripboard designs
    [BaseCom.brd, BaseCom.sch, Simple Multiplexer.sch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]
2020-05-29 Designed Pod v1 in Altium. Reorganised stripboard designs into EAGLE folder.
    [2-PLCC LED.PcbLib, 2-PLCC LED.SchLib, BaseCom.brd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]
2020-06-22 Fixed short between 5V_servo and GND present on v1.0
    [Pod.PcbDoc]
2020-06-22 Updated README and gitignore
    [Pod.PcbDoc]
2020-11-25 Added dimensions and decriptions to Pod PCB document. Created STEP file of the Gimbal.
    [FrSky M9 Gimbal.SLDPRT, FrSky M9 Gimbal.STEP, Pod.PcbDoc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]
2020-11-27 Made modifications to the Adafruit SSD1306 library to allow it to work for the SSD1362. This does come with a number of bugs and is currently not fully functional.
    [ssd1362_256x64_spi.ino]
2020-11-28 Improved processing of stick inputs and properly constrained PWM outputs. Increased trim hold delay when it is 0.
2020-11-28 Added frame synchronisation test.
2020-12-03 Fixed stick input direction scaling.
    [CRASH.ino]
2020-12-03 Added actual range of PWM values
2020-12-04 Added functionality to measure battery voltage
2020-12-05 Update README.md
    Added TODO and CRASH board, including hardware issues
2020-12-08 Added battery level indicator bar and value to display.
2021-01-28 Implemented acknowledgement (ack) packets and packet loss and ping metrics. Replaced delay() with an interval. Packet loss is currently not necessarily indicative of the main packet because the ACK i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
    [CRASH.ino, Pod.ino]
2021-02-06 Added reading and storage of sensor values to csv files.
2021-02-06 Added separate timer for when the display gets updated.
2021-02-06 Made screen turn off after 30 seconds to prevent damage to the OLED. Also changed ping to be in ms, rather than us.
    [Display.cpp]
2021-02-06 Stopped SD card reinitialization if it disconnects. This means the device needs to be restarted if the SD card disconnects. However, doing this prevents the device lagging due to the time it takes to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
    [CRASH.ino]
2021-02-08 Inverted inputs, increased number of trim steps to 100, added warning light if radio fails to begin, changed radio address, updated BMP3XX library to 2.0.2 and changed startNewFile() to void.
    [CRASH.ino, Display.cpp, Pod.ino]
2021-02-08 Added units to csv file of stored data. Also changed to storing pressure, rather than altitude.
2021-02-08 Fixed trim still being inverted.
    [CRASH.ino]
2021-08-01 Added Crash flight computer Altium files.
    [B12B-PH-K-S(LF)(SN).PcbLib, B12B-PH-K-S(LF)(SN).SchLib, CRASH_Inputs.PrjPcb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]

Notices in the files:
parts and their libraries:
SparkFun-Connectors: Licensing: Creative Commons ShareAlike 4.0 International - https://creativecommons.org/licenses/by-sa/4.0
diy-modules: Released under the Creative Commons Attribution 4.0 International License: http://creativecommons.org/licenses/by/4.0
